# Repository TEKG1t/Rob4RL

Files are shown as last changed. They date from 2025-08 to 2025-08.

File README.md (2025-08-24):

# Rob4RL - Robot for Reinforcement Learning

Rob4RL is a student project which aims to explore the feasibilty of low-cost bipedal robotics for the learning robust, sim2real applicable reinforcement learning based locomotion policies.

It has been built upon the work of David Ho, the original creator of the Legolas bipedal walker.

<p align="center">
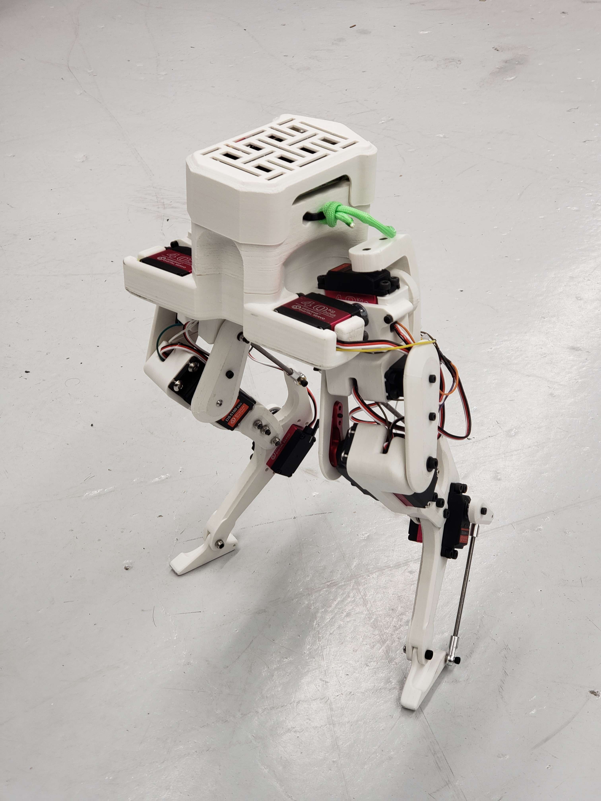
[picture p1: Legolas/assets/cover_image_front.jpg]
  
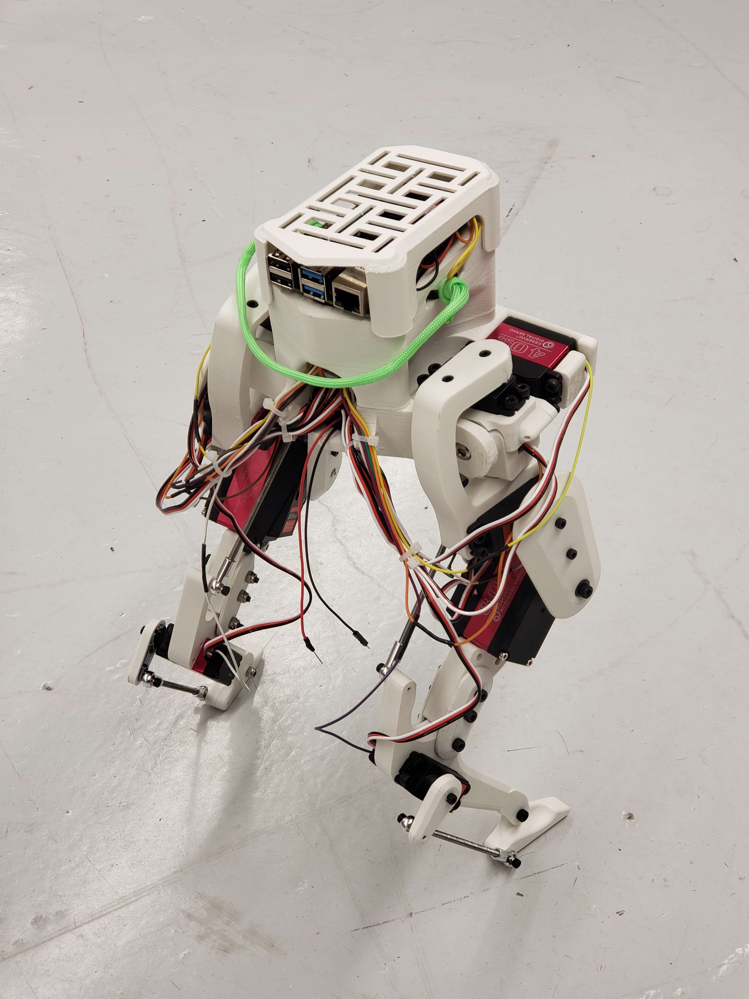
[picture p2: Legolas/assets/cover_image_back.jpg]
  
</p>

## Repository Contents

This repository contains forked CAD and 3D printing files for Legolas.

It also contains small calibration/test python code snippets for I2C communication and test of the servos. Note that the current control code is only on prototype level - use with caution.

It will be updated regulary with the likes of model-based control, simulation testing and RL training code, likely in Isaac Sim/Lab.

Original Robot Design [Legolas Robot](https://github.com/daviddoo02/Legolas-an-open-source-biped/).

Original Robot Code [Legolas Controller](https://github.com/daviddoo02/Legolas_Controller).

## Getting Started

1. **Clone this repository:**

    ```bash
    git clone https://github.com/TEKG1t/Rob4RL.git
    ```

2. **Modify CAD or 3D Print the robot:**
  - Original SolidWorks files are provided in `Legolas/CAD` for modification
  - STL files are located in `Legolas/STLs` to 3D print your own robot, see assembly instuctions

3. **Assemble the robot**
  - See assembly instuctions

4. **TODO Next Steps**
  - Lets see if I am allowed to upload the intermediate milestone paper :)
  - Modified main body, actuator model for servos and model-based control

<p align="center">
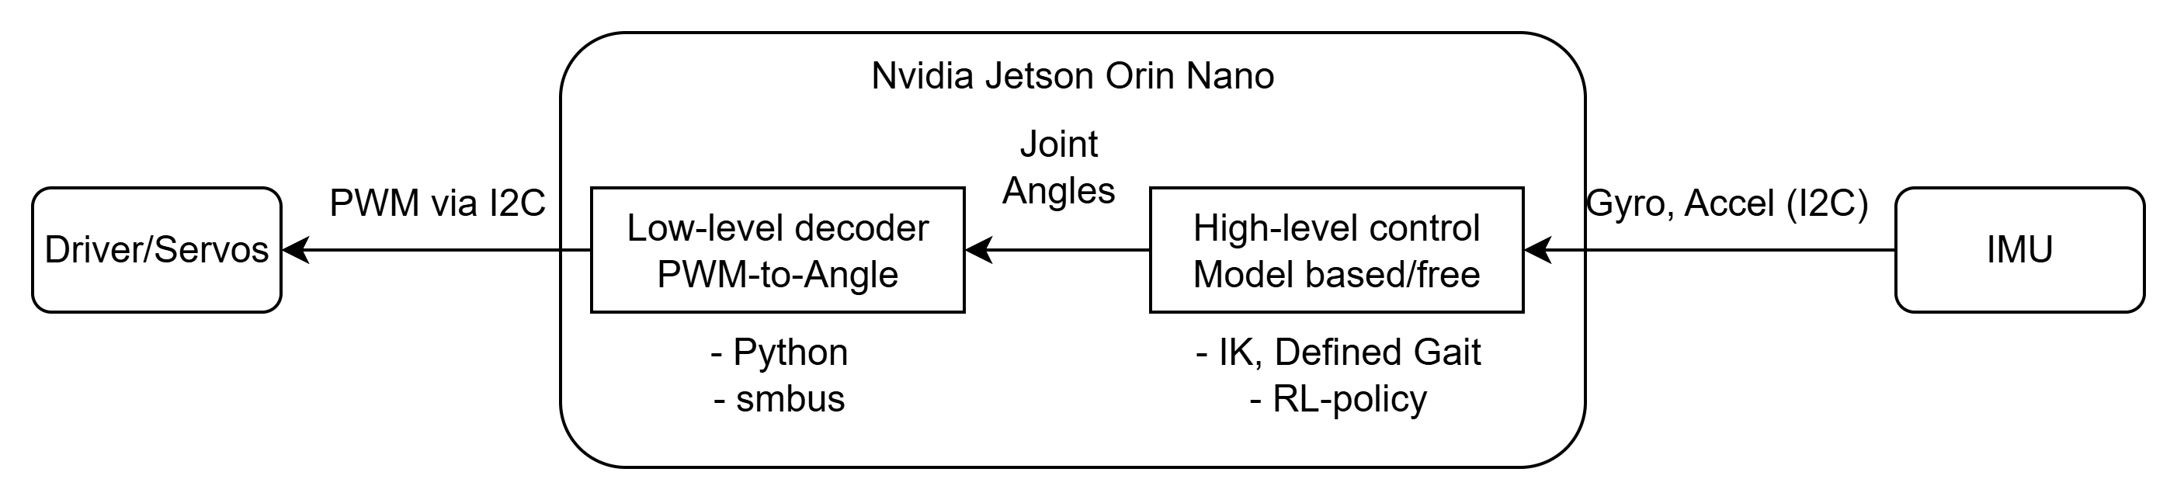
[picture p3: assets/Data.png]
  
</p>

## Required Materials

Original BOM with Amazon Links is shown in the original README of the Legolas Robot.

My Robot is using a Nvidia Jetson Orin Nano Super DevKit as Controller although a simple RL policy should be able to run on a raspy as well.

I am using 35kgcm instead of 40kgcm and 60kgcm instead of 80kgcm servos of similar standardized size because of hardware availability.

| **Type** | **Specification** | **Value** |
|---|---|---|
| | Height | 50cm |
| General | Weight | 3kg |
| | Material | PLA |
| | Cost | 1500€ |
| | Name | Nvidia Jetson Orin Nano |
| Controller | Storage | 500GB NVME M.2 |
| | 35kgcm Servo | 8120MG 180° |
| Actuators | 60kgcm Servo | DS5160 SSG 270° |
| | Servo driver | PCA9685 |
| Sensors | IMU | MPU6050 |

Note: General Robot values are estimates for now.

## Assembly Instruction

This section summarizes the assembly of one Legolas left leg.  

### 3D Printing BOM
Start by printing the STL files under `Legolas/STLs`. Some parts need to be mirrored for the right leg. Optional TPU shoes can be added for extra grip.

| **Part Name** | **Amount** | **Mirror for right leg** |
|---|---|---|
| Main body.stl | 1 | |
| Hip 1 A.stl | 1 | x |
| Hip 1 B.stl | 1 | x |
| Hip 2.stl or Pitch A + B | 1 | x |
| Thigh Inner.stl | 1 | |
| Thigh Outer.stl | 1 | |
| Foreleg A.stl | 1 | x |
| Foreleg B + C.stl | 1 | |
| Shin.stl | 1 | |
| Servo Cover.stl | 1 | |
| Foot.stl | 1 | x | 

Recommended print settings (I used Cura):
- Walls: min 4 lines for strength  
- Infill: slightly higher than default  
- Wall order: inside → outside  

One leg weighs ~184g, takes ~15h to print, and ~2–3h to assemble.  

### Servo & Mechanical Assembly
Each leg uses:
- 3 × 40 kg·cm servos (hip)  
- 1 × 80 kg·cm servo (knee)  
- 1 × 40 kg·cm servo (foot)  

Prototype tested with 35 kg·cm and 60 kg·cm servos (still compatible).  
Cut threaded rods to:  
- 85 mm (upper transmission bar)  
- 80 mm (lower bar)  

Refer to the hardware BOM for screws, nuts, and bearings.
All screws default to cylinder head unless specified. Slight over-provisioning ensures successful assembly during prototyping. The original designer recommends purchasing a metric nuts and bolts assortment kit.

| **Amount** | **Part Name** | **Usage** |
|---|---|---|
| 6 | AXK0619 Bearings | Joints |
| 4 | M4 ball rod ends | Joint transmission |
| 2 | M4 threaded rod | Joint transmission; cut to length  |
| 5 | M3x8 | Servo shaft to servo |
| 5 | M3x10 | Servo shaft to print |
| 4 | M3x16 | Hip 2 A+B |
| 1 | M3x20 | Foot servo shaft |
| 1 | M3x25 drop forge screw | Hip-thigh rod |
| 16 | M4x12 | 35kgcm servo mounting |
| 2 | M4x20 | Passive hip-thigh joint |
| 2 | M4x35 | Foreleg-shin joint |
| 1 | M4x40 | Final foreleg-shin joint |
| 4 | M5x12 | 60kgcm servo mounting |
| 1 | M6x16 | Hip joint |
| 1 | M6x16 drop forge screw | Hip joint |
| 2 | M3 locking nuts | Shaft and joint locking |
| 5 | M4 locking nuts | Transmission/bar locking |
| 6–11 | M4 nuts | Transmission/bar locking |
| 2 | M6 locking nuts | Hip joint mounting |
| 3 | M3 washers | Passive joint load distribution |
| 1 | M4 washer | Passive joint load distribution |

Use zip ties or wraps for cable management. See assembly image for reference.  

<p align="center">
  
</p>

## License

This project is licensed under the MIT License - see the [LICENSE](LICENSE) file for details.

## Acknowledgments

- Thanks to Berkeley Humanoid (Lite) projects which inspired this research
- Thanks to David Ho, the original creator of the Legolas robot
- The Legolas robot is inspired by the Cassie robot by Agility Robotics.

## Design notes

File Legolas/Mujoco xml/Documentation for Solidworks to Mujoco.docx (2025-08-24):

Documentation for Solidworks to Mujoco:

1. Exporting from Solidworks using SW2URDF:
  a. Step 1: Download SW2URDF extension
    i. Repo: https://github.com/ros/solidworks_urdf_exporter/releases
  b. Step 2: Assigning frames to your robot
    i. (170) Frame Assignment For Robotic Manipulators - Direct Kinematics I - YouTube (https://www.youtube.com/watch?v=fNIyNF87q9I&t=244s)
    ii. ^ this video should give you a good idea of what assigning frames is and how to know where to place your frames.
    iii. Use the Reference geometry → Coordinate system tool in Solidworks.
      1. A useful tip: Point your coordinate systems toward each other if possible – this will make it easier to code in mujoco later.
  c. Step 3: Using the extension
    i. Follow this video tutorial: https://www.youtube.com/watch?v=ge3P307TgJI
    ii. Now you should have a folder with the URDF of your robot.
2. Accessing the URDF and verifying the urdf:
  a. Ref:
    i. https://mujoco.readthedocs.io/en/latest/modeling.html#curdf
    ii. urdf - ROS Wiki (http://wiki.ros.org/urdf)
  b. Step 1: Checking if your URDF generated correctly:
    i. Add the mujoco extension after robot name like so:

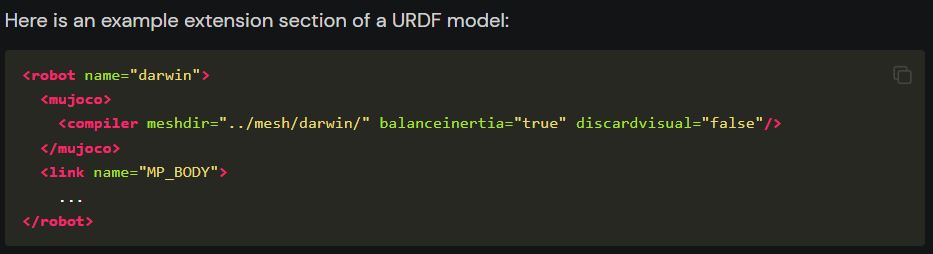
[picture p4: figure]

  c. Step 2: Check the URDF for collision/joint problems:
    i. After you add the extension, you should be able to drag and drop the file into mujoco and 2 things can happen:
      1. Everything runs < less interesting
      2. Everything runs itself apart < more interesting
        a. If this was the case, you could be running into a collision issue.
        b. You can confirm this by tapping F to toggle the forces vectors and H to toggle the convex hull

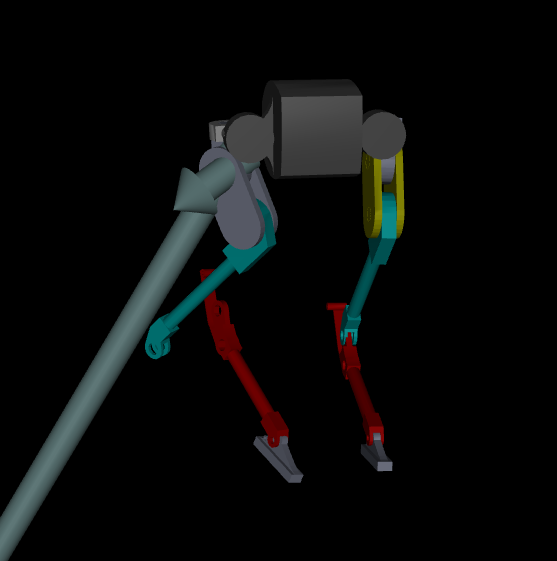
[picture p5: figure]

          ii. So, as you can see, there is a huge force coming off the body and the knee joint not being connected.
    ii. Fixing Joints:
      1. Go back to Solidworks and check how the urdf was generated, make sure all the frames and joint types are correct and regenerate the urdf.
    iii. Fixing collision:
      1. Check which part is colliding by hitting the H-key on your keyboard.
        a. Note: if a collision geometry was not specified, mujoco will automatically generate it, but it messes up sometimes.
      2. Solution: in the URDF, replace the collision mesh with something else by changing the name of the collision geometry mesh to the new mesh.
  d. Step 3: Verifying your URDF on Linux:
    i. Use the following command on Linux terminal to verify the URDF:
      1. rosrun urdfdom check_urdf /path2model/<model>.urdf
    ii. This should output the kinematic tree of your robot.

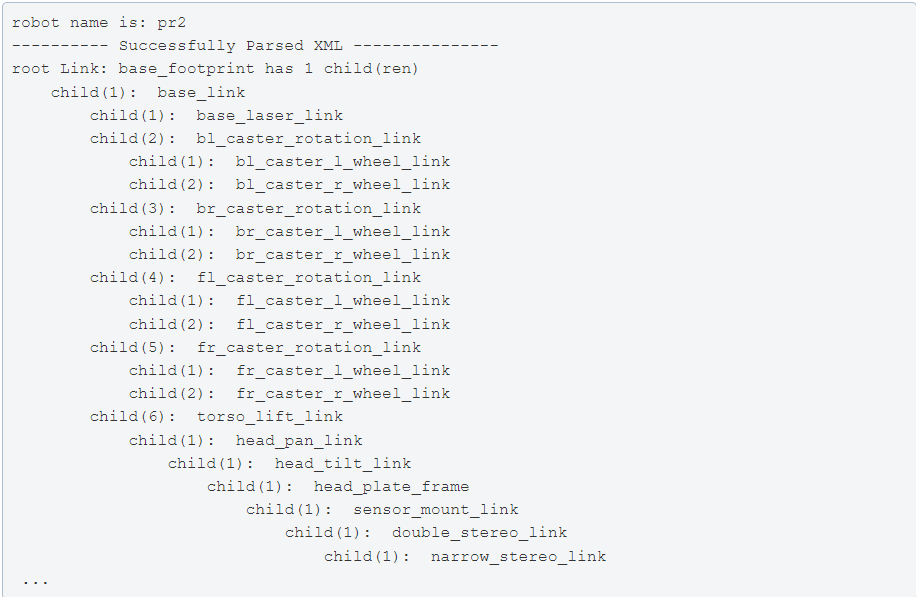
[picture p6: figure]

3. Converting URDF to MUJOCO xml:
  a. Ref:
    i. wangcongrobot/dual_ur5_husky_mujoco: Dual UR5 Husky Robot MuJoCo Model (github.com) (https://github.com/wangcongrobot/dual_ur5_husky_mujoco)
  b. Enter the path ~/mujoco/mujoco200/bin first and run command below:
  c. Convert the urdf:
    i. compile /path/to/model.urdf /path/to/model.xml
  d. Test:
    i. mujoco200/bin$ ./simulate /path/to/model.xml

Congratulations! You are now able to run mujoco with your robot design! Add more mujoco tags as needed

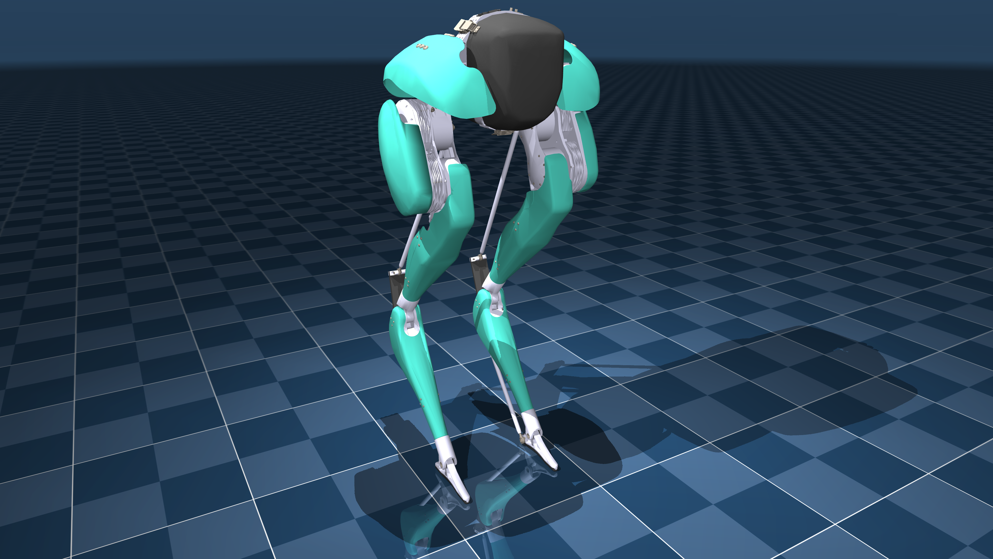
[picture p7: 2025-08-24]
Legolas/Mujoco xml/References/agility_cassie/cassie.png

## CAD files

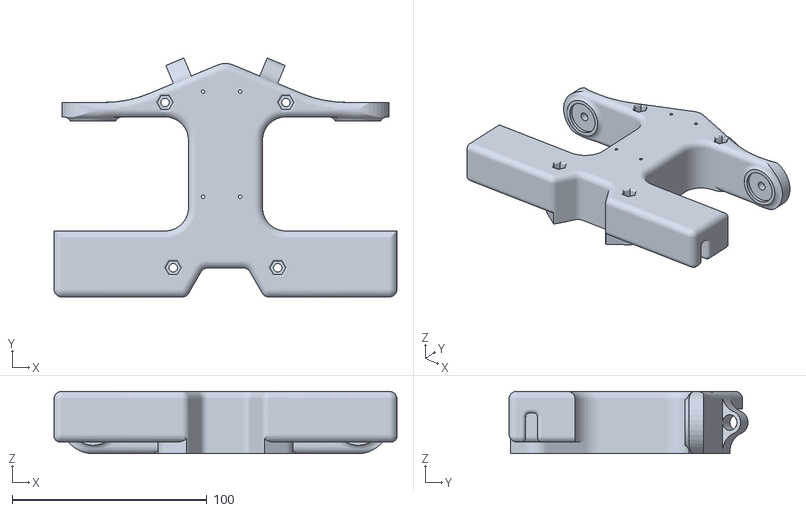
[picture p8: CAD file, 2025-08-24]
Legolas/STLs/Main body.STL
176.0 x 122.7 x 32.0

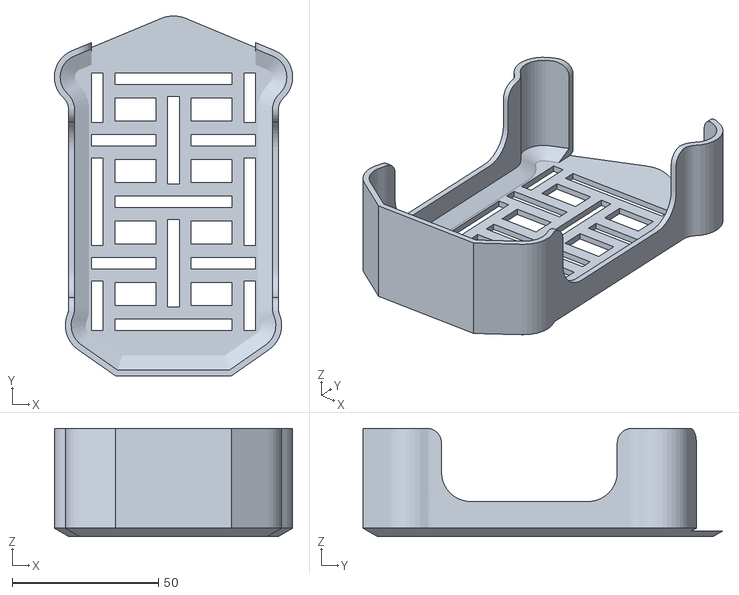
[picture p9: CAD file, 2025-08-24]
Legolas/STLs/Main body cover.STL
81.4 x 122.9 x 37.0

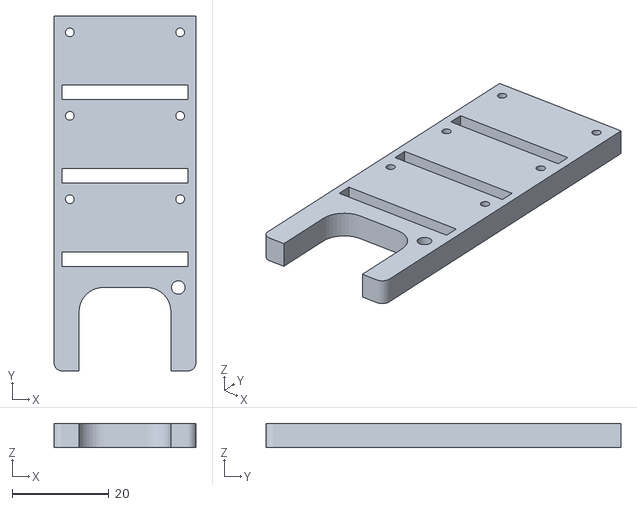
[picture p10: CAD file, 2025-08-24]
Legolas/STLs/Main body ADC Mount.STL
29.4 x 73.5 x 5.00

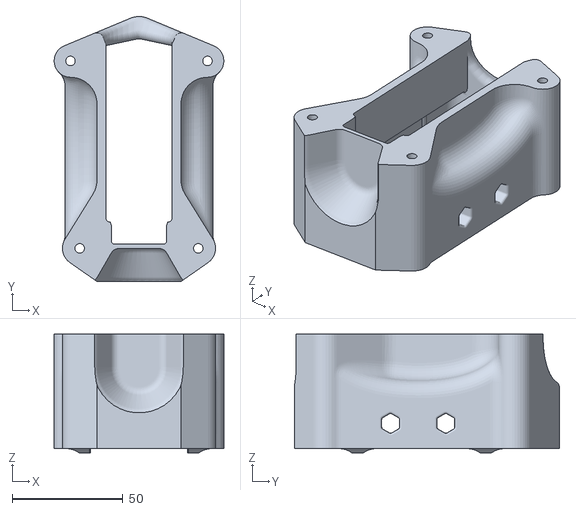
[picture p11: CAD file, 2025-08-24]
Legolas/STLs/Main body Wire Connector Container.STL
76.8 x 119.9 x 53.8

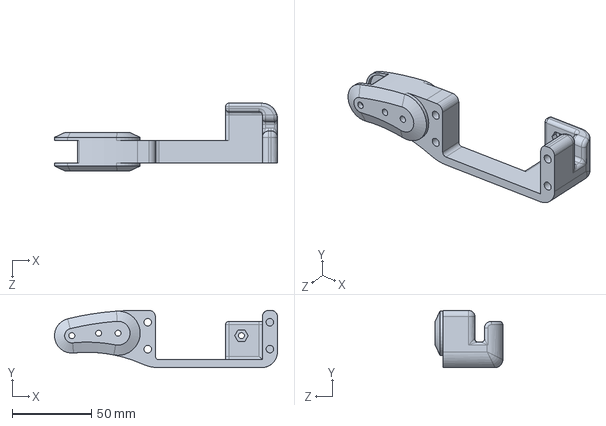
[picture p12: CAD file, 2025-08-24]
Legolas/CAD/Legolas/V3/Foreleg v3.SLDPRT
141.0 x 36.2 x 42.8 mm

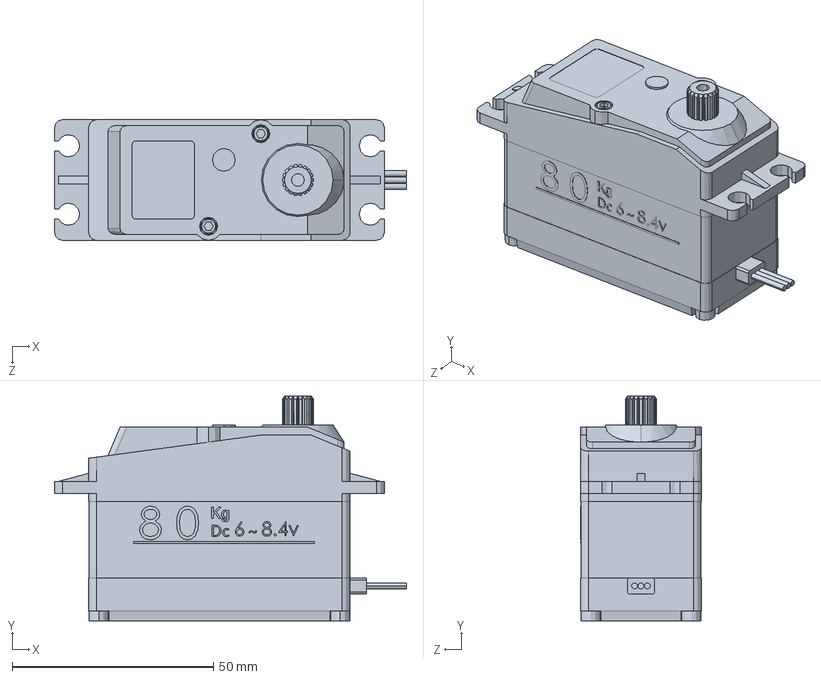
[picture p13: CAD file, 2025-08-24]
Legolas/CAD/Servo and electronics/80kg_servo.SLDPRT
87.5 x 55.9 x 30.0 mm

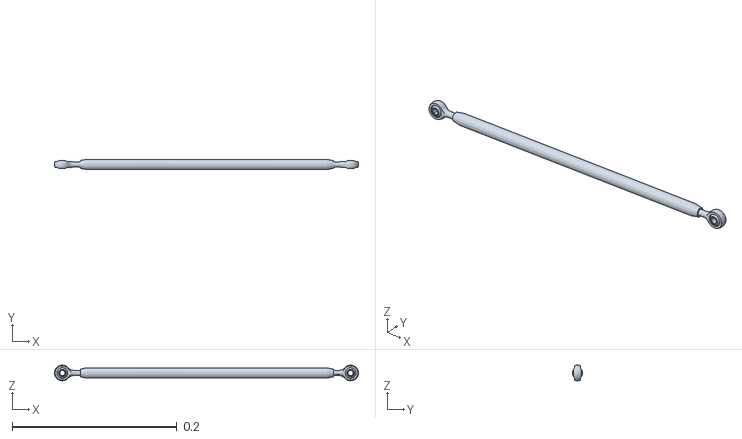
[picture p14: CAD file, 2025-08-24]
Legolas/Mujoco xml/References/agility_cassie/assets/plantar-rod.obj
0.369 x 0.0127 x 0.0191

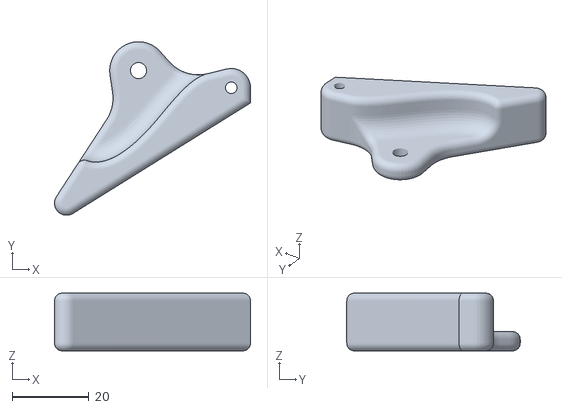
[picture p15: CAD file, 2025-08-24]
Legolas/STLs/Foot.STL
50.9 x 45.1 x 15.0

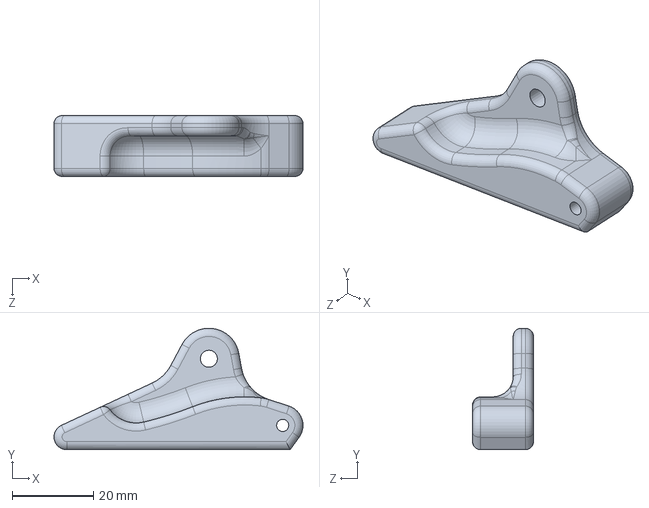
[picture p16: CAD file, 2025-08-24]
Legolas/CAD/Legolas/V3/Foot v3.SLDPRT
61.3 x 29.9 x 15.0 mm

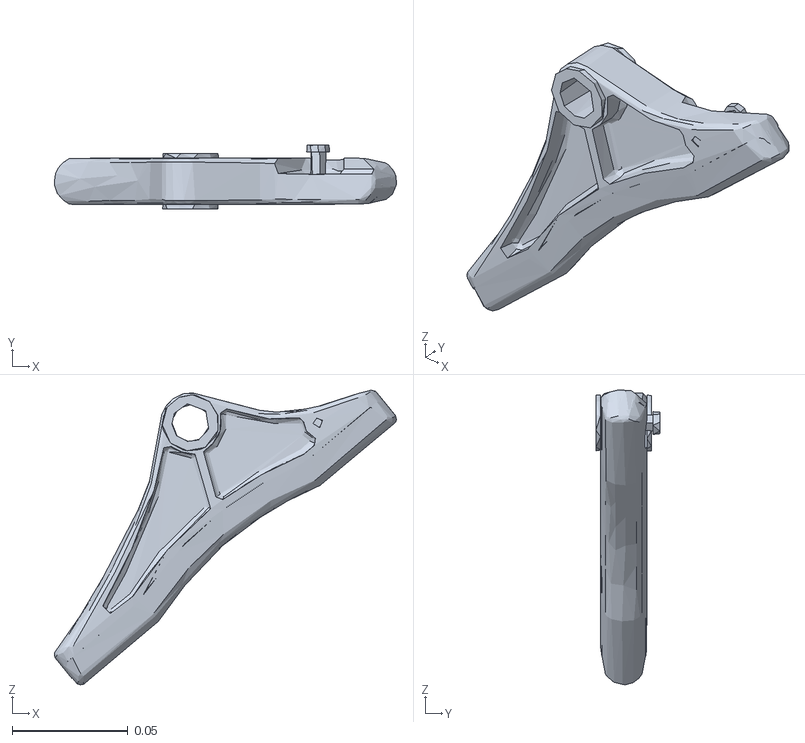
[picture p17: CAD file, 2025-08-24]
Legolas/Mujoco xml/References/agility_cassie/assets/foot.obj
0.148 x 0.0277 x 0.127

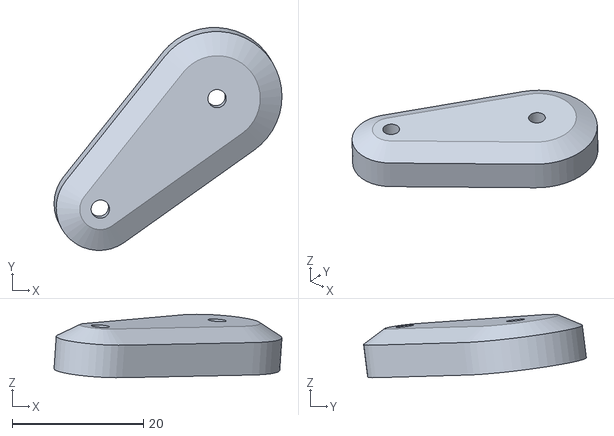
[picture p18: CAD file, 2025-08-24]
Legolas/STLs/Servo Cover.STL
34.7 x 34.0 x 9.67

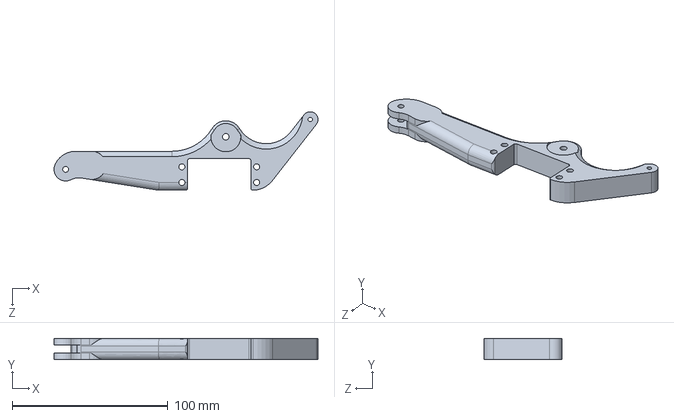
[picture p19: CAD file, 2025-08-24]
Legolas/CAD/Legolas/V3/Shin v3.SLDPRT
169.4 x 13.7 x 50.4 mm

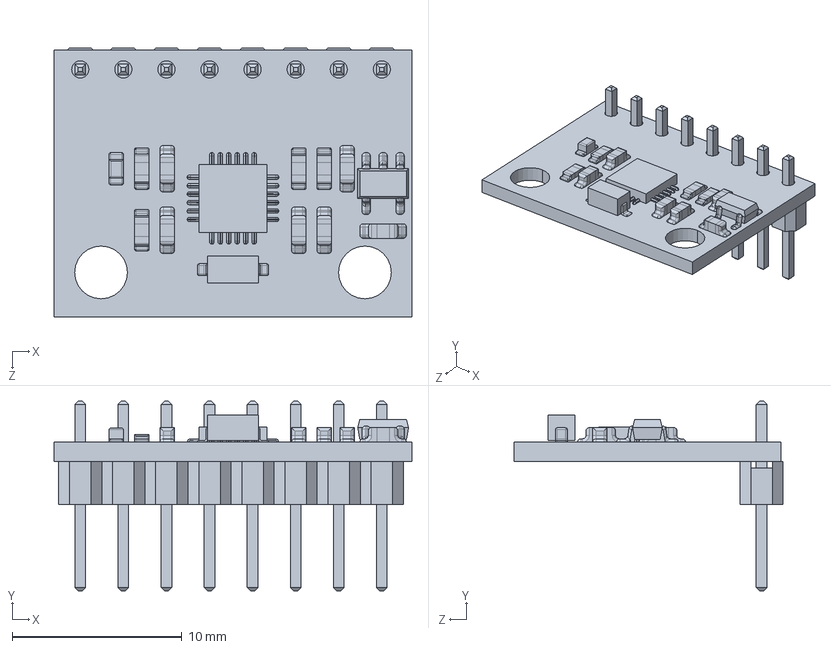
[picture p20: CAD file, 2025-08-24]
Legolas/CAD/Servo and electronics/MPU 6050 IMU.SLDPRT
21.1 x 11.2 x 15.9 mm

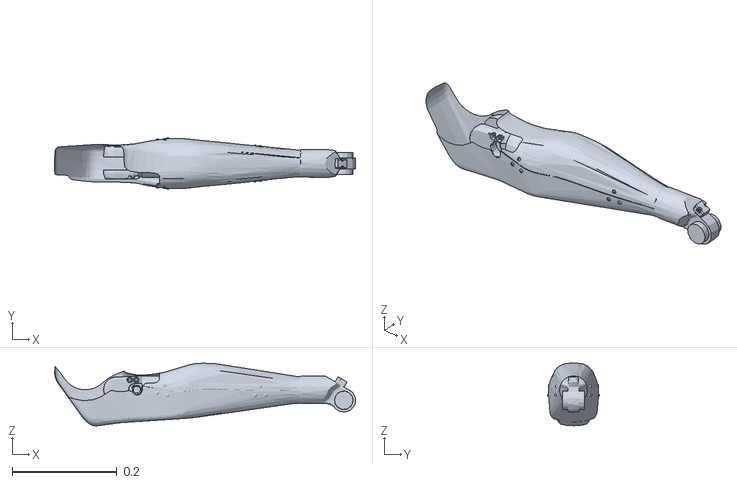
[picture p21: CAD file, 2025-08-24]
Legolas/Mujoco xml/References/agility_cassie/assets/shin.obj
0.576 x 0.0987 x 0.12

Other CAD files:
Legolas/CAD/Test_Bench/Test_Bench_Mk2.SLDASM
Legolas/CAD/Servo and electronics/servo.SLDASM
Legolas/CAD/Servo and electronics/Mirror40 kg Servo Arm.SLDPRT
Legolas/STLs/Shoe B.STL
Legolas/CAD/Legolas/V2/Foot.SLDPRT
Legolas/CAD/Legolas/V2/Foreleg.SLDPRT
Legolas/CAD/Legolas/V2/Hip Pitch.SLDPRT
Legolas/CAD/Legolas/V2/Hip Roll.SLDPRT
Legolas/CAD/Legolas/V2/Hip Yaw.SLDPRT
Legolas/CAD/Legolas/V2/Servo Cover.SLDPRT
Legolas/CAD/Legolas/V2/Shin.SLDPRT
Legolas/CAD/Legolas/V2/Thigh Inner.SLDPRT
Legolas/CAD/Legolas/V2/Thigh Outer.SLDPRT
Legolas/CAD/Legolas/V2/Thrust Bearing.SLDASM
Legolas/CAD/Legolas/V2/right_leg_redundant/Legolas V2 Right Leg.SLDASM
Legolas/CAD/Legolas/V2/right_leg_redundant/MirrorFoot.SLDPRT
Legolas/CAD/Legolas/V2/right_leg_redundant/MirrorForeleg.SLDPRT
Legolas/CAD/Legolas/V2/right_leg_redundant/MirrorHip Pitch.SLDPRT
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

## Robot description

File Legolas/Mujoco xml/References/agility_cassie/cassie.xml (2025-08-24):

<mujoco model="cassie">
  <compiler eulerseq="zyx" meshdir="assets" texturedir="assets" autolimits="true"/>

  <option timestep="0.0005"/>
  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

  <default>
    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
    <equality solref="0.005 1"/>
    <default class="cassie">
      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
    </default>
    <default class="collision">
      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
      <default class="collision-left">
        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
      </default>
      <default class="collision-right">
        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
      </default>
    </default>
  </default>

  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

  <worldbody>
    <light name="spotlight" mode="targetbodycom" target="cassie-pelvis" pos="0 -1 2"/>
    <body name="cassie-pelvis" pos="0 0 1.1" childclass="cassie">
      <camera name="track" pos="0 -3 1" zaxis="0 -1 0.5" mode="track"/>
      <inertial pos="0.05066 0.000346 0.02841" mass="10.33" fullinertia="0.085821 0.049222 0.08626 1.276e-05 -0.00016022 -0.000414"/>

      <freejoint/>

      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
      
      <body name="left-hip-roll" pos="0.021 0.135 0" xyaxes="0 0 -1 0 1 0">
        <inertial pos="-0.01793 0.0001 -0.04428" mass="1.82" fullinertia="0.003431 0.003793 0.002135 -6.65e-07 -0.00084 3.99e-06"/>
        <joint name="left-hip-roll" type="hinge" range="-15 22.5" damping="1" armature="0.038125"/>
        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
        <body name="left-hip-yaw" pos="0 0 -0.07" xyaxes="0 0 1 0 1 0">
          <inertial pos="0 -1e-05 -0.034277" mass="1.171" fullinertia="0.002443 0.002803 0.000842 -4e-08 2.462e-07 -2.71e-08"/>
          <joint name="left-hip-yaw" type="hinge" range="-22.5 22.5" damping="1" armature="0.038125"/>
          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
          <body name="left-hip-pitch" pos="0 0 -0.09" xyaxes="0 0 -1 1 0 0">
            <inertial pos="0.05946 5e-05 -0.03581" mass="5.52" fullinertia="0.010898 0.029714 0.030257 -0.0002669 -5.721e-05 9.17e-06"/>
            <joint name="left-hip-pitch" type="hinge" range="-50 80" damping="1" armature="0.09344"/>
            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
            <body name="left-achilles-rod" pos="0 0 0.045" xyaxes="0.7922 -0.60599 -0.072096 0.60349 0.79547 -0.054922">
              <inertial pos="0.24719 0 0" mass="0.1567" fullinertia="3.754e-06 0.004487 0.004488 -3.74e-08 -1.61e-08 0"/>
              <joint name="left-achilles-rod" type="ball" damping="0.01"/>
              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
            </body>
            <body name="left-knee" pos="0.12 0 0.0045" xyaxes="0.70711 -0.70711 0 0.70711 0.70711 0">
              <inertial pos="0.023 0.03207 -0.002181" mass="0.7578" fullinertia="0.001376 0.0010335 0.0021637 -0.00039744 -4.085e-05 -5.374e-05"/>
              <joint name="left-knee" type="hinge" ref="-45" range="-164 -37" damping="1" armature="0.09344"/>
              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
              <body name="left-knee-spring" pos="0.06068 0.08241 0">
                <inertial pos="0.0836 0.0034 0" mass="0.186" fullinertia="5.215e-05 0.00041205 0.0003669 6.87e-06 0 0"/>
                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
              </body>
              <body name="left-shin" pos="0.06068 0.04741 0">
                <inertial pos="0.18338 0.001169 0.0002123" mass="0.577" fullinertia="0.00035939 0.014728 0.014707 -0.00020981 2.266e-05 -1.2e-07"/>
                <joint name="left-shin" type="hinge" range="-20 20" stiffness="1500" damping="0.1"/>
                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
                <body name="left-tarsus" pos="0.43476 0.02 0" xyaxes="0.52992 0.84805 0 -0.84805 0.52992 0">
                  <inertial pos="0.11046 -0.03058 -0.00131" mass="0.782" fullinertia="0.00039238 0.013595 0.013674 0.00023651 -4.987e-05 -4.82e-06"/>
                  <joint name="left-tarsus" type="hinge" ref="58" range="50 170" damping="0.1"/>
                  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
                  <body name="left-heel-spring" pos="-0.01269 -0.03059 0.00092" xyaxes="-0.91211 0.40829 0.036948 -0.40992 -0.90952 -0.068841">
                    <inertial pos="0.081 0.0022 0" mass="0.126" fullinertia="2.959e-05 0.00022231 0.0002007 7.15e-06 -6e-07 1e-07"/>
                    <joint name="left-heel-spring" type="hinge" stiffness="1250"/>
                    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
                  </body>
                  <body name="left-foot-crank" pos="0.058 -0.034 0.02275">
                    <inertial pos="0.00493 2e-05 -0.00215" mass="0.1261" fullinertia="2.6941e-05 4.9621e-05 6.3362e-05 -2.1e-09 -3.9623e-06 -1.09e-08"/>
                    <joint name="left-foot-crank" type="hinge" range="-140 -30" damping="1"/>
                    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
                    <body name="left-plantar-rod" pos="0.055 0 -0.00791">
                      <inertial pos="0.17792 0 0" mass="0.1186" fullinertia="2.779e-06 0.001774 0.001775 -2.34e-08 -8.1e-09 0"/>
                      <joint name="left-plantar-rod" type="hinge"/>
                      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
                    </body>
                  </body>
                  <body name="left-foot" pos="0.408 -0.04 0">
                    <inertial pos="0.00474 0.02748 -0.00014" mass="0.1498" fullinertia="0.00017388 0.00016793 0.00033261 0.00011814 1.36e-06 -4e-07"/>
                    <joint name="left-foot" type="hinge" range="-140 -30" damping="1" armature="0.01225"/>
                    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
                  </body>
                </body>
              </body>
            </body>
          </body>
        </body>
      </body>
      <body name="right-hip-roll" pos="0.021 -0.135 0" xyaxes="0 0 -1 0 1 0">
        <inertial pos="-0.01793 0.0001 -0.04428" mass="1.82" fullinertia="0.003431 0.003793 0.002135 6.65e-07 -0.00084 -3.99e-06"/>
        <joint name="right-hip-roll" type="hinge" range="-22.5 15" damping="1" armature="0.038125"/>
        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
        <body name="right-hip-yaw" pos="0 0 -0.07" xyaxes="0 0 1 0 1 0">
          <inertial pos="0 1e-05 -0.034277" mass="1.171" fullinertia="0.002443 0.002803 0.000842 4e-08 2.462e-07 2.71e-08"/>
          <joint name="right-hip-yaw" type="hinge" range="-22.5 22.5" damping="1" armature="0.038125"/>
          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
          <body name="right-hip-pitch" pos="0 0 -0.09" xyaxes="0 0 -1 1 0 0">
            <inertial pos="0.05946 5e-05 0.03581" mass="5.52" fullinertia="0.010898 0.029714 0.030257 -0.0002669 5.721e-05 -9.17e-06"/>
            <joint name="right-hip-pitch" type="hinge" range="-50 80" damping="1" armature="0.09344"/>
            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
            <body name="right-achilles-rod" pos="0 0 -0.045" xyaxes="0.7922 -0.60599 0.072096 0.60349 0.79547 0.054922">
              <inertial pos="0.24719 0 0" mass="0.1567" fullinertia="3.754e-06 0.004487 0.004488 -3.74e-08 1.61e-08 0"/>
              <joint name="right-achilles-rod" type="ball" damping="0.01"/>
              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
            </body>
            <body name="right-knee" pos="0.12 0 -0.0045" xyaxes="0.70711 -0.70711 0 0.70711 0.70711 0">
              <inertial pos="0.023 0.03207 0.002181" mass="0.7578" fullinertia="0.001376 0.0010335 0.0021637 -0.00039744 4.085e-05 5.374e-05"/>
              <joint name="right-knee" type="hinge" ref="-45" range="-164 -37" damping="1" armature="0.09344"/>
              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
              <body name="right-knee-spring" pos="0.06068 0.08241 0">
                <inertial pos="0.0836 0.0034 0" mass="0.186" fullinertia="5.215e-05 0.00041205 0.0003669 6.87e-06 0 0"/>
                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
              </body>
              <body name="right-shin" pos="0.06068 0.04741 0">
                <inertial pos="0.18338 0.001169 -0.0002123" mass="0.577" fullinertia="0.00035939 0.014728 0.014707 -0.00020981 -2.266e-05 1.2e-07"/>
                <joint name="right-shin" type="hinge" range="-20 20" stiffness="1500" damping="0.1"/>
                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
                <body name="right-tarsus" pos="0.43476 0.02 0" xyaxes="0.52992 0.84805 0 -0.84805 0.52992 0">
                  <inertial pos="0.11046 -0.03058 0.00131" mass="0.782" fullinertia="0.00039238 0.013595 0.013674 0.00023651 4.987e-05 4.82e-06"/>
                  <joint name="right-tarsus" type="hinge" ref="58" range="50 170" damping="0.1"/>
                  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
                  <body name="right-heel-spring" pos="-0.01269 -0.03059 -0.00092" xyaxes="-0.91211 0.40829 -0.036948 -0.40992 -0.90952 0.068841">
                    <inertial pos="0.081 0.0022 0" mass="0.126" fullinertia="2.959e-05 0.00022231 0.0002007 7.15e-06 6e-07 -1e-07"/>
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

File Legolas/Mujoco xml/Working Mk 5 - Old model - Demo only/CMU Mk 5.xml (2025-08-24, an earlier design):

<mujoco model="CMU Mk 5">
  <compiler angle="radian" meshdir="meshes/" autolimits="true"/>
  
  <option timestep="0.005" gravity="0 0 0"/>

  <default/>

  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
  
  <worldbody>
    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
    
    <light name="spotlight" mode="targetbodycom" target="base link" pos="0 6 4" castshadow="false"/>
    
    <body name="base link" pos="0 0 .2">    
      <camera name="track" pos="0 -3 1" zaxis="0 -1 0.5" mode="track"/>
      <inertial pos="0 0 0" mass="0.0299227589680342" fullinertia="4.64430780114595E-06 4.78982197003375E-06 5.96248441172554E-06 -7.0005651433527E-12 1.45948993644989E-11 -7.65792898200085E-08"/>
      
      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      
      
      <body name="R_Hip_1" pos="0.021005 0 0" quat="0.706765 0.706768 -0.0219327 0.0219327">
        <inertial pos="-3.00471e-07 -4.83658e-06 0.00581975" quat="0.707107 0 0 0.707107" mass="0.000490673" diaginertia="1.27003e-08 9.79961e-09 4.84291e-09"/>
        
        <joint name="R_Hip_1" type="hinge" pos="0 0 0" axis="0 0 1"/>
        
        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
        
        <body name="R_Hip_2" pos="0 0 0.0076962" quat="0.529268 0.52927 0.468907 -0.468908">
          <inertial pos="-1.39156e-10 -1.14679e-09 0.0107683" quat="0.707107 0 0 0.707107" mass="0.00100456" diaginertia="4.56705e-08 3.43974e-08 1.53565e-08"/>
          
          <joint name="R_Hip_2" type="hinge" pos="0 0 0" axis="0 0 1"/>
          
          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
          
          <body name="R_Thigh" pos="0 0 0.013139" quat="0.397507 0.584796 0.584798 0.397509">
            <inertial pos="3.40459e-05 0.009 0" quat="0.707107 0.707107 0 0" mass="0.00259524" diaginertia="2.57116e-07 2.17945e-07 5.47709e-08"/>
            
            <joint name="R_Thigh" type="hinge" pos="0 0 0" axis="-1 0 0"/>
            
            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
            
            <body name="R_Foreleg" pos="0 0.018 0" quat="-1.92102e-06 3.13083e-06 -0.852343 0.522982">
              <inertial pos="0 0.0208617 -0.00148561" quat="0.684738 0.728789 0 0" mass="0.00244939" diaginertia="1.23016e-06 1.2006e-06 3.92157e-08"/>
              
              <joint name="R_Foreleg" type="hinge" pos="0 0 0" axis="-1 0 0" limited="true" range="-5 100" damping="0"/>
              
              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

              <body name="R_Shin" pos="0 0.064516 0" quat="0.868737 -0.495274 0 0">
                <inertial pos="4.16582e-05 0.0220307 -0.00550832" quat="0.819399 0.572189 -0.0177322 0.029512" mass="0.00129205" diaginertia="4.33834e-07 4.29412e-07 9.31982e-09"/>
                
                <joint name="R_Shin" type="hinge" pos="0 0 0" axis="-1 0 0"/>
                
                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

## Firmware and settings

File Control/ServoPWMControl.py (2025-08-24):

##
#- Low level Servo PWM control using the PCA9685
##    

import time
import math
from smbus2 import SMBus

# --- PCA9685 low-level control class ---
class PCA9685:
    MODE1 = 0x00
    PRESCALE = 0xFE
    LED0 = 0x06

    def __init__(self, bus_num=7, addr=0x40, freq=50):
        self.bus = SMBus(bus_num)
        self.addr = addr
        self.set_pwm_freq(freq)

    def write8(self, reg, val):
        self.bus.write_byte_data(self.addr, reg, val)

    def read8(self, reg):
        return self.bus.read_byte_data(self.addr, reg)

    def set_pwm_freq(self, freq_hz):
        # Formula from datasheet
        prescale = int(math.floor(25_000_000 / (4096 * freq_hz) - 0.5))
        old = self.read8(self.MODE1)
        self.write8(self.MODE1, (old & 0x7F) | 0x10)  # sleep
        self.write8(self.PRESCALE, prescale)
        self.write8(self.MODE1, old)
        time.sleep(0.005)
        self.write8(self.MODE1, old | 0x80)

    def set_pwm(self, channel, on, off):
        self.write8(self.LED0 + 4*channel    , on & 0xFF)
        self.write8(self.LED0 + 4*channel +1 , (on >> 8) & 0xFF)
        self.write8(self.LED0 + 4*channel +2 , off & 0xFF)
        self.write8(self.LED0 + 4*channel +3 , (off >> 8) & 0xFF)

    def pulse_us_to_ticks(self, pulse_us, freq_hz=50):
        period_us = 1_000_000 / freq_hz
        return int(round(pulse_us / period_us * 4096))

# --- Example usage ---
if __name__ == "__main__":
    pca = PCA9685(bus_num=7, addr=0x40, freq=50)
    channel = 0

    # Example PWM bounds (adjust later)
    servo_min = 1000  # µs
    servo_mid = 1500  # µs (rest)
    servo_max = 2000  # µs

    print("Sweeping from min to max pulse")
    for pulse in (servo_min, servo_mid, servo_max):
        ticks = pca.pulse_us_to_ticks(pulse)
        pca.set_pwm(channel, 0, ticks)
        print(f"Pulse: {pulse} μs → Ticks: {ticks}")
        time.sleep(1)

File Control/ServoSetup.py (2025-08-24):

##
#- Initializes the servo (I2C with PCA9685)
#- Waits for user input from the terminal
#- Validates and caps the angle between 0 and 180
#- Moves the servo to the input angle
#- Waits briefly before prompting for the next input
##    

from adafruit_servokit import ServoKit
import board
import busio
import time

# Initialize I2C bus and ServoKit
i2c_bus = busio.I2C(board.SCL, board.SDA)
kit = ServoKit(channels=16, i2c=i2c_bus)

print("ServoKit initialized. Ready for angle input (0–180).")

while True:
    try:
        user_input = input("Enter angle (0–180) or 'q' to quit: ").strip()
        
        if user_input.lower() == 'q':
            print("Exiting.")
            break
        
        angle = int(user_input)

        # Cap the angle between 0 and 180
        angle = max(0, min(180, angle))
        
        # Move the servo (on channel 0)
        kit.servo[0].angle = angle
        print(f"Moved servo to {angle} degrees.")

        time.sleep(0.5)  # Short delay before next input

    except ValueError:
        print("Invalid input. Please enter a number between 0 and 180, or 'q' to quit.")

            

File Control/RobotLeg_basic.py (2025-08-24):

### INITIAL DOC
## Power dist (DC, shared GND)
# - 35kgcm is 4.8~8.4V; 60kgcm is 6~8.4V
# - PCA9685 logic is 3.3V, power is max 5V -> Too weak for Servos
# - PCA9685 to Servo only for PWM, 8V Servo power line seperately (buck converter?)
# - MAX Current draw in theory: 
#
## Channel desc
#- (35kgcm) [0-2]   Hip roll/pitch/jaw 
#- (60kgcm) [3]     Knee
#- (35kgcm) [4]     Foot
#
## Brief Building instructions
#- Refer to Legolas Biped GitHub for basic part CAD setup (STL/Solidworks)
#- Printing was done in PLA with more wall layers/infill (probably better: PETG/ABS)
#- Set servos to 90° (ideally real life correction) before assembly
#- Part assembly with direct screwing, locking nuts (M2, M3, M4)
###

### SOFTWARE
#- UI with sliders for each DOF and Sweep switch (max current draw est)
#- There seems to be a bug where servo [2] could not stop sweeping

import tkinter as tk
from tkinter import messagebox
from adafruit_servokit import ServoKit
import board
import busio
import threading
import time

# Initialize I2C and ServoKit
i2c_bus = busio.I2C(board.SCL, board.SDA)
kit = ServoKit(channels=16, i2c=i2c_bus)

#For Button control
def set_all_servos(angle):
    for i in range(5):
        # Skip if sweep is active for a servo
        _, var = sweep_checkboxes[i]
        if not var.get():
            kit.servo[i].angle = angle
            update_ui(i, angle)

# Function to update servo angle from slider
def update_servo_angle(servo_index, angle):
    angle = int(angle)
    kit.servo[servo_index].angle = angle
    update_ui(servo_index, angle)

# Function to handle editable angle field input
def set_angle_from_entry(servo_index):
    try:
        angle = int(entry_fields[servo_index].get())
        if 0 <= angle <= 180:
            kit.servo[servo_index].angle = angle
            update_ui(servo_index, angle)
        else:
            messagebox.showwarning("Invalid Angle", "Please enter an angle between 0 and 180.")
    except ValueError:
        messagebox.showwarning("Invalid Input", "Please enter a valid integer.")


# Function to handle the sweep checkbox
def toggle_sweep(servo_index):
    _, var = sweep_checkboxes[servo_index]
    is_sweeping = var.get()

    if is_sweeping:
        # Disable UI while sweeping
        entry_fields[servo_index].config(state=tk.DISABLED)
        sliders[servo_index].config(state=tk.DISABLED)

        # Start a thread that loops the sweep
        def sweep_loop():
            while var.get():
                for angle in range(0, 181, 2):
                    kit.servo[servo_index].angle = angle
                    update_ui(servo_index, angle)
                    time.sleep(0.02)
                    if not var.get():
                        break
                for angle in range(180, -1, -2):
                    kit.servo[servo_index].angle = angle
                    update_ui(servo_index, angle)
                    time.sleep(0.02)
                    if not var.get():
                        break
            # Re-enable UI when done
            update_ui(servo_index)

        t = threading.Thread(target=sweep_loop, daemon=True)
        t.start()
        sweep_threads[servo_index] = t
    else:
        # Sweep thread will stop and update_ui will re-enable inputs
        pass

def update_ui(servo_index, angle=None):
    # If no angle provided, use last known slider value
    if angle is None:
        angle = kit.servo[servo_index].angle or 0

    angle = int(angle)

    # Update angle display in entry field
    entry_fields[servo_index].config(state=tk.NORMAL)
    entry_fields[servo_index].delete(0, tk.END)
    entry_fields[servo_index].insert(0, str(angle))

    # Update slider position
    sliders[servo_index].config(state=tk.NORMAL)
    sliders[servo_index].set(angle)

    # Disable entry + slider if sweep is active
    _, var = sweep_checkboxes[servo_index]
    if var.get():
        entry_fields[servo_index].config(state=tk.DISABLED)
        sliders[servo_index].config(state=tk.DISABLED)

### UI

# Create main Tkinter window
root = tk.Tk()
root.title("3D-Druck Dulli Leg Controller")
root.geometry("500x600")
root.resizable(False, False)

# Add global control buttons
button_frame = tk.Frame(root)
button_frame.pack(pady=10)

reset_btn = tk.Button(button_frame, text="Reset (90°)", command=lambda: set_all_servos(90), width=12)
reset_btn.grid(row=0, column=0, padx=5)

min_btn = tk.Button(button_frame, text="Min (0°)", command=lambda: set_all_servos(0), width=12)
min_btn.grid(row=0, column=1, padx=5)

max_btn = tk.Button(button_frame, text="Max (180°)", command=lambda: set_all_servos(180), width=12)
max_btn.grid(row=0, column=2, padx=5)


# Label for the headline
#headline = tk.Label(root, text="3D-Druck Dulli Leg Controller", font=("Arial", 18), anchor="w")
#headline.pack(fill=tk.X, padx=10, pady=10)

servo_names = [
    "Hip roll",
    "Hip pitch",
    "Hip yaw",
    "Knee",
    "Foot"
]
angle_labels = []  # Labels to display the angle
entry_fields = []  # Entry fields for angle input
sweep_checkboxes = []  # Checkbox for servo sweep
sweep_threads = [None] * 5  # List to keep track of threads for sweep mechanism
sliders = []

# Create UI for each servo
for i in range(5):
    frame = tk.Frame(root)
    frame.pack(fill=tk.X, padx=10, pady=5)

    # Line 1: Name, Current Angle, and Sweep checkbox
    name_label = tk.Label(frame, text=servo_names[i], font=("Arial", 12))
    name_label.grid(row=0, column=0, padx=5, pady=5)

    # Entry field for editable angle input
    entry_field = tk.Entry(frame, width=5)
    entry_field.insert(0, "90")  # Default angle is 90 degrees
    entry_field.grid(row=0, column=2, padx=5, pady=5)
    entry_fields.append(entry_field)

    # Sweep checkbox
    sweep_var = tk.BooleanVar()
    sweep_checkbox = tk.Checkbutton(frame, text="Sweep", variable=sweep_var, command=lambda i=i: toggle_sweep(i))
    sweep_checkbox.grid(row=0, column=3, padx=5, pady=5)
    sweep_checkboxes.append((sweep_checkbox, sweep_var))  # store both


    # Line 2: Slider for adjusting servo angle
    slider = tk.Scale(frame, from_=0, to=180, orient=tk.HORIZONTAL, length=200, command=lambda val, i=i: update_servo_angle(i, val))
    slider.set(90)  # Default slider value is 90 degrees
    slider.grid(row=1, column=0, columnspan=4, padx=5, pady=5)
    sliders.append(slider)


    # Bind the entry field to update angle when edited
    entry_field.bind("<Return>", lambda event, i=i: set_angle_from_entry(i))

# Start the Tkinter event loop
print("Starting PCA9685 Servo Control UI...")
root.mainloop()
